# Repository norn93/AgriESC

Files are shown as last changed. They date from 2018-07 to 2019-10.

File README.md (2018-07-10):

# AgriESC
A brushless motor driver for small to medium sized motors

This project was forked from and inspired by antonchromjak's MINI4 (Mini VESC: https://github.com/antonchromjak/MINI4) and was practically copied from Benjamin Vedder's Brushless Motor Controller (VESC: https://github.com/vedderb/bldc-hardware). It is an attempt to build a slightly cheaper motor controller for 24 V/10 A motors.

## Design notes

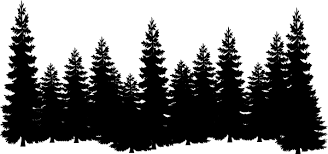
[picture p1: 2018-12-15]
images/forest.png

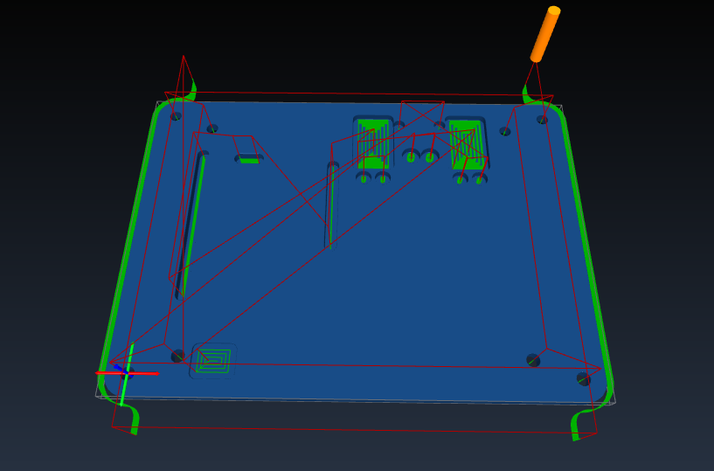
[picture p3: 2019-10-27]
gcode/Heatsink/heatsink.png

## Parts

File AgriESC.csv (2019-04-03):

Id | Designator | Package | Quantity | Designation | Supplier and ref
1 | R42,R43,R20,R21,R35 | R_0603_1608Metric_Pad1.05x0.95mm_HandSolder | 5 | 10k
2 | U16 | SOT-23-5 | 1 | MCP6001-OT
3 | USB | CONN-10118194-0001LF-FCI3 | 1 | USB_OTG
4 | C7,C8 | CP_Radial_D10.0mm_P5.00mm_Side_Mounted | 2 | 680u_35V
5 | R25 | R_0603_1608Metric_Pad1.05x0.95mm_HandSolder | 1 | 0R
6 | R26,R28 | R_0603_1608Metric_Pad1.05x0.95mm_HandSolder | 2 | 22R
7 | REF**,REF**,REF**,REF** | MountingHole_3.2mm_M3_Pad_Via | 4 | MountingHole_3.2mm_M3_Pad_Via
8 | SWD | JST_PA_01x05 | 1 | SWD
9 | COMM | JST_PA_01x08 | 1 | COMM
10 | C27,C12,C13,C14,C15,C16,C26 | C_0603_1608Metric_Pad1.05x0.95mm_HandSolder | 7 | 100n
11 | HALL ENCODERS | JST_PA_01x06 | 1 | HALL_ENC
12 | CAN | JST_PA_01x04 | 1 | CAN
13 | U1,U2,U3,U4,U5,U6 | FDMS7698 | 6 | FDMS7698
14 | GPIO | JST_PA_01x06 | 1 | GPIO
15 | U15,U14 | SOT-23 | 2 | MCP1700-3302E_SOT23
16 | U10 | LQFP-64_10x10mm_P0.5mm | 1 | STM32F405RGT6
17 | D2 | LED_0603_1608Metric_Pad1.05x0.95mm_HandSolder | 1 | GREEN
18 | Y1 | CSTNE8M00G550000R0 | 1 | 8M Resonator
19 | C1,C2,C3,C4,C5,C6,C41 | C_0805_2012Metric_Pad1.15x1.40mm_HandSolder | 7 | 4u7_35V
20 | C9,C10,C11 | C_0603_1608Metric_Pad1.05x0.95mm_HandSolder | 3 | 0.1u
21 | C17,C18,C19,C20,C21,C25,C28,C29,C30 | C_0603_1608Metric_Pad1.05x0.95mm_HandSolder | 9 | 2u2
22 | C22,C23,C24 | C_0603_1608Metric_Pad1.05x0.95mm_HandSolder | 3 | 4n7
23 | C31,C33,C36 | C_0603_1608Metric_Pad1.05x0.95mm_HandSolder | 3 | 100n_16V
24 | C32 | C_0603_1608Metric_Pad1.05x0.95mm_HandSolder | 1 | 22n_50V
25 | C34 | C_0603_1608Metric_Pad1.05x0.95mm_HandSolder | 1 | 2u2_16V
26 | C35 | C_0603_1608Metric_Pad1.05x0.95mm_HandSolder | 1 | 220n_16V
27 | C37 | C_0603_1608Metric_Pad1.05x0.95mm_HandSolder | 1 | 100n_6V3
28 | C38 | C_0603_1608Metric_Pad1.05x0.95mm_HandSolder | 1 | 1u_6V3
29 | C39,C46 | C_0603_1608Metric_Pad1.05x0.95mm_HandSolder | 2 | 100n_10V
30 | C40 | C_0603_1608Metric_Pad1.05x0.95mm_HandSolder | 1 | 1u_10V
31 | C42 | C_0603_1608Metric_Pad1.05x0.95mm_HandSolder | 1 | 470n_35V
32 | C43,C44,C49,C51 | C_0603_1608Metric_Pad1.05x0.95mm_HandSolder | 4 | 2u2_5V
33 | C45 | C_0603_1608Metric_Pad1.05x0.95mm_HandSolder | 1 | 100n_5V
34 | C47 | C_0603_1608Metric_Pad1.05x0.95mm_HandSolder | 1 | 2u2_35V
35 | C48 | C_0603_1608Metric_Pad1.05x0.95mm_HandSolder | 1 | 10u_5V
36 | C50,C52 | C_0603_1608Metric_Pad1.05x0.95mm_HandSolder | 2 | 2u2_3V3
37 | D1 | LED_0603_1608Metric_Pad1.05x0.95mm_HandSolder | 1 | BLUE
38 | D3 | LED_0603_1608Metric_Pad1.05x0.95mm_HandSolder | 1 | RED
39 | D4 | D_SOD-123F | 1 | D_Schottky_40V_1A
40 | J1 | XT30PW-F | 1 | SUPPLY
41 | A | SolderWirePad_1x01_SMD_5x10mm | 1 | PH_A
42 | B | SolderWirePad_1x01_SMD_5x10mm | 1 | PH_B
43 | C | SolderWirePad_1x01_SMD_5x10mm | 1 | PH_C
44 | SERVO | JST_PA_01x03 | 1 | SERVO
45 | L1 | NR8040T220M | 1 | 22u
46 | R1,R2,R3,R10,R11,R12 | R_0603_1608Metric_Pad1.05x0.95mm_HandSolder | 6 | 4R7
47 | R4,R5,R6 | R_2512_6332Metric_Pad1.52x3.35mm_HandSolder | 3 | 0.004R
48 | R7,R8,R9 | R_0603_1608Metric_Pad1.05x0.95mm_HandSolder | 3 | 59k
49 | R13,R14,R15 | R_0603_1608Metric_Pad1.05x0.95mm_HandSolder | 3 | 1k
50 | R16,R17,R18,R22 | R_0603_1608Metric_Pad1.05x0.95mm_HandSolder | 4 | 100R
51 | R19 | R_0603_1608Metric_Pad1.05x0.95mm_HandSolder | 1 | 10k_NTC
52 | R23,R24 | R_0603_1608Metric_Pad1.05x0.95mm_HandSolder | 2 | 150R
53 | R27,R31,R36,R39 | R_0603_1608Metric_Pad1.05x0.95mm_HandSolder | 4 | 47k
54 | R29 | R_0603_1608Metric_Pad1.05x0.95mm_HandSolder | 1 | 220R
55 | R30,R32,R38,R40 | R_0603_1608Metric_Pad1.05x0.95mm_HandSolder | 4 | 5k6
56 | R33,R34,R37 | R_0603_1608Metric_Pad1.05x0.95mm_HandSolder | 3 | 2k2
57 | R41 | R_0603_1608Metric_Pad1.05x0.95mm_HandSolder | 1 | 100k
58 | U7,U8,U9 | MAX9920 | 3 | MAX9920
59 | U11 | DRV8303 | 1 | DRV8303
60 | U13 | SOT-23-6 | 1 | LMR16006YQ5
61 | U12 | DFN-8-1EP_3x3mm_Pitch0.65mm | 1 | TJA1051TK-3
62 | NT1,NT2,NT3 | NetTie-2_SMD_Pad0.5mm | 3 | Net-Tie_2
63 | SW1 | SolderJumper-3_P1.3mm_Open_RoundedPad1.0x1.5mm_NumberLabels | 1 | SW_SPDT
64 | REF** | OSHW-Logo_7.5x8mm_SilkScreen | 1 | OSHW-Logo_7.5x8mm_SilkScreen
65 | G*** | LOGO3 | 1 | LOGO3

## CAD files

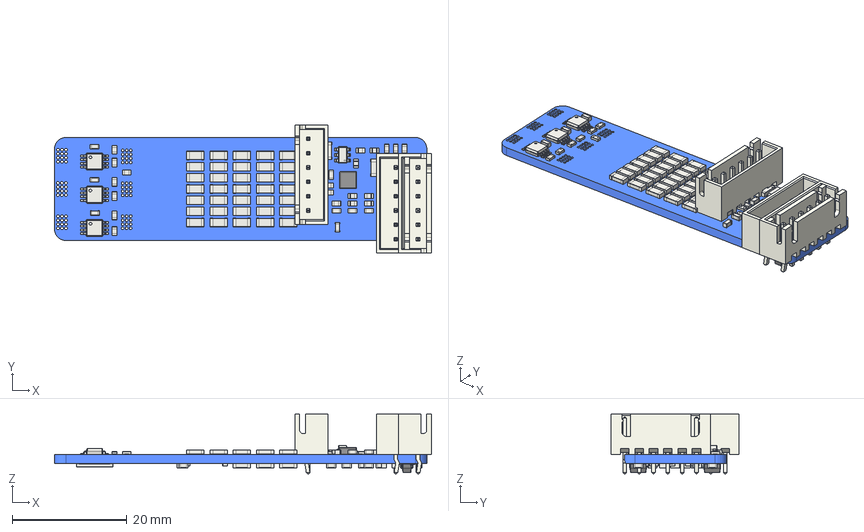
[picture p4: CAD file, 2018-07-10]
mini4/MINI_VESC.FCStd
65.8 x 22.4 x 10.4 mm
Pcb
C_1206_
R_0603_
C_0603_
R_0603_001
R_0603_002
R_0603_003
C_0603_001
R_0603_004
R_0603_005
C_1206_001
C_1206_002
C_1206_003
C_1206_004
C_1206_005
C_1206_006
C_1206_007
C_1206_008
C_1206_009
C_1206_010
C_1206_011
C_1206_012
C_1206_013
C_1206_014
C_1206_015
C_1206_016
C_1206_017
C_1206_018
C_1206_019
C_1206_020
C_1206_021
C_1206_022
C_1206_023
C_1206_024
C_1206_025
C_1206_026
C_1206_027
C_1206_028
C_1206_029
C_1206_030
C_1206_031
C_1206_032
C_1206_033
C_1206_034
C_1206_035
C_1206_036
C_1206_037
C_0603_002
C_0603_003
R_0603_006
R_0603_007
R_0603_008
R_0603_009
R_0603_010
R_0603_011
SOT_23_6_
R_0603_012
R_0603_013
C_1206_038
C_1206_039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

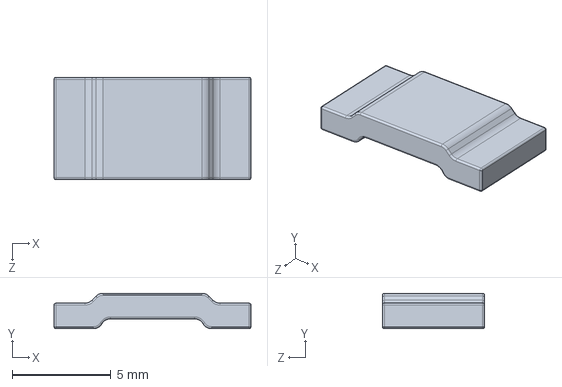
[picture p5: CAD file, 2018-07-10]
mini4_3dmodels/3921_RESISTOR.STEP
10.0 x 1.80 x 5.20 mm

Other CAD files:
mini4_3dmodels/user library-pqfn 5x6.wrl.sldprt
mini4_3dmodels/pqfn 5x6.wrl.sldprt

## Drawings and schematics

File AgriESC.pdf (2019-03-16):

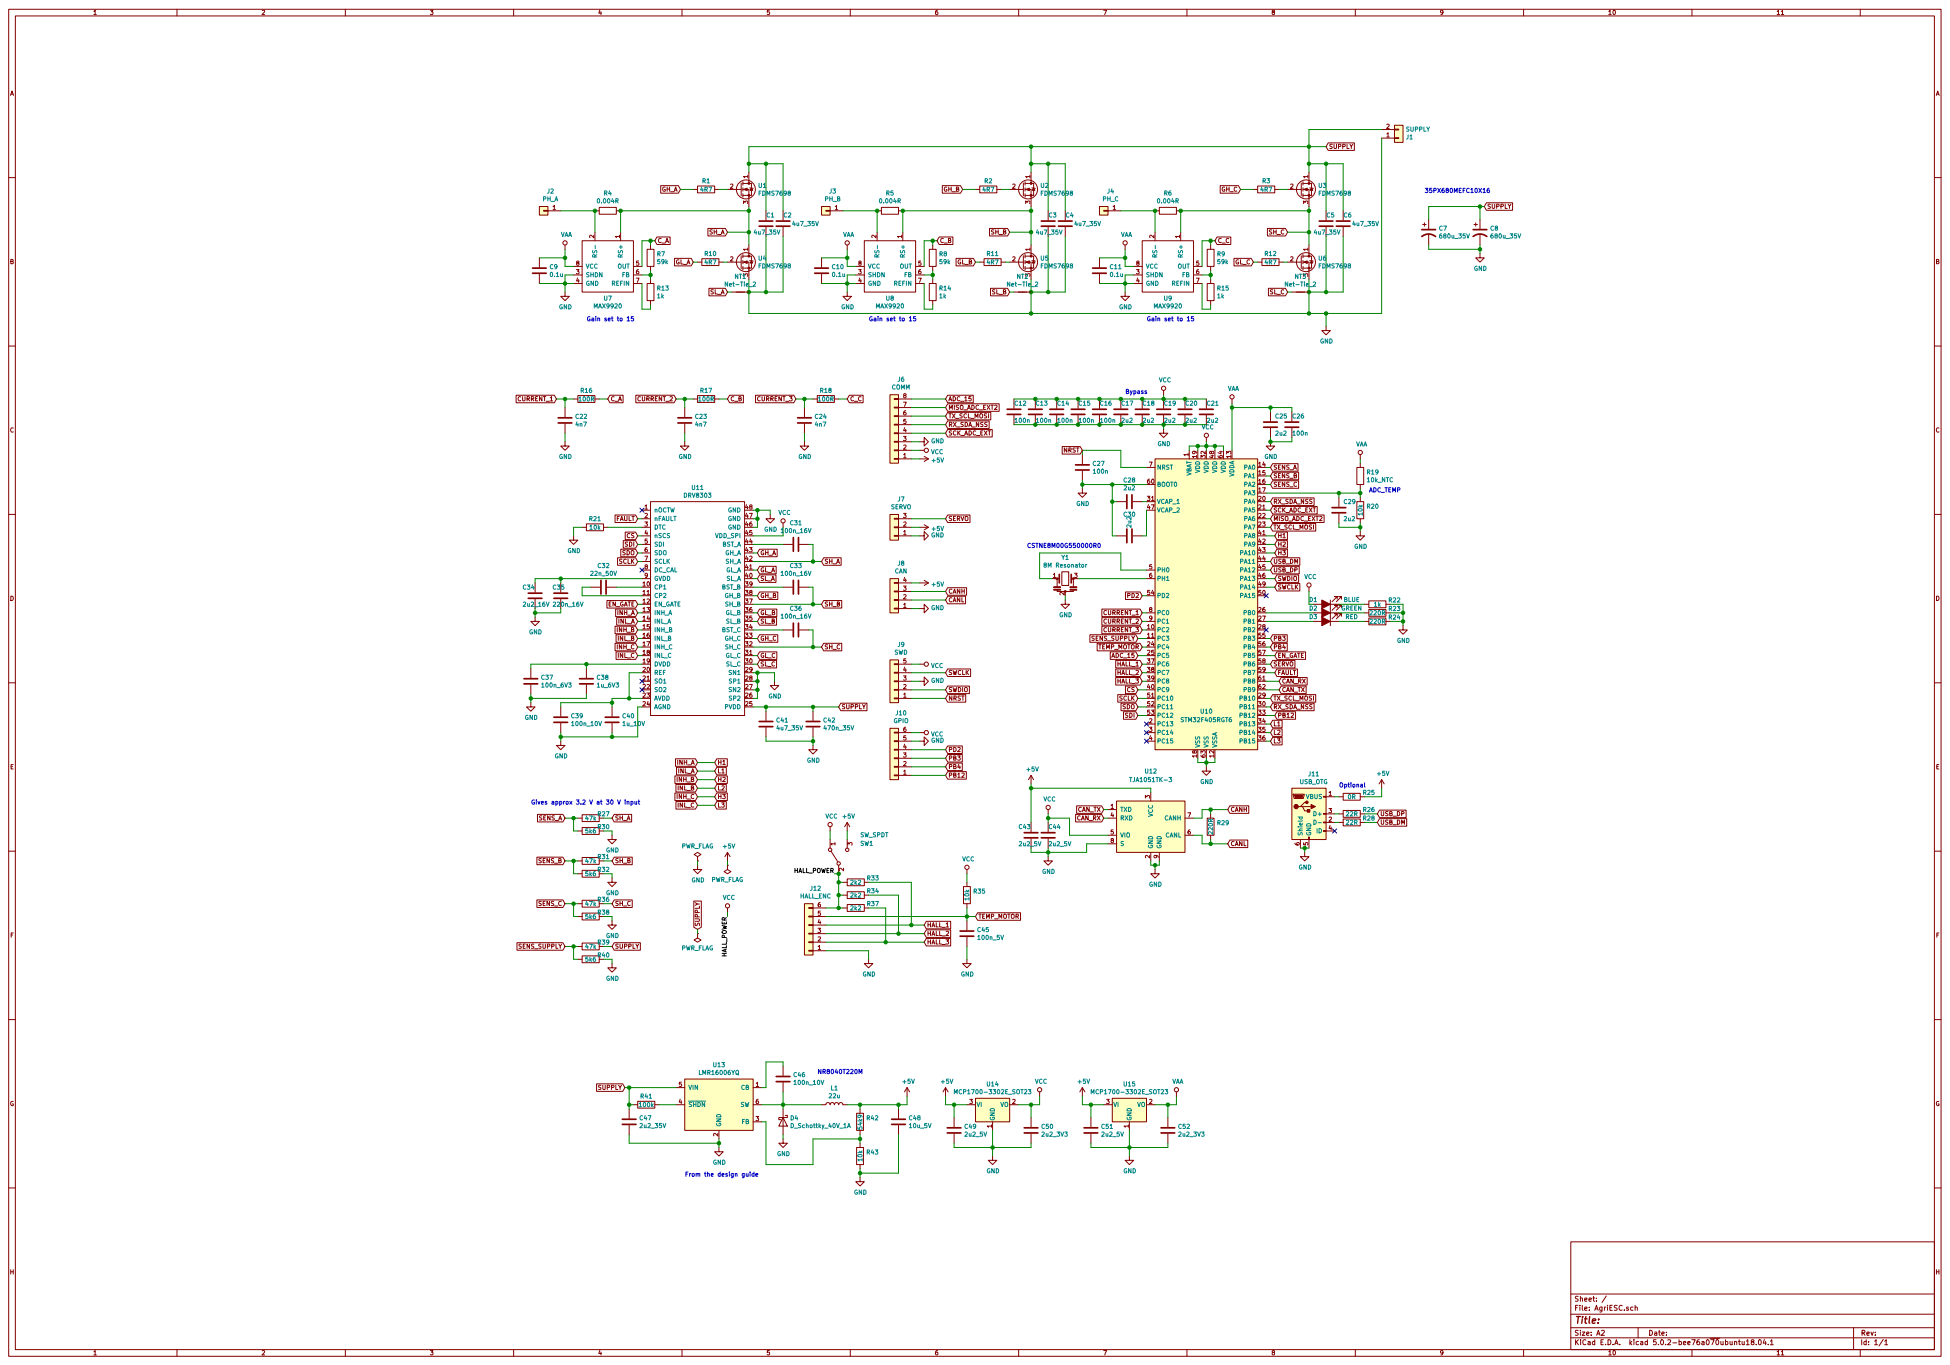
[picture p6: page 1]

PD2 PB3 PB4 PB12 +5V GND GND Gives approx 3.2 V at 30 V input C37

File: AgriESC.sch Sheet: /

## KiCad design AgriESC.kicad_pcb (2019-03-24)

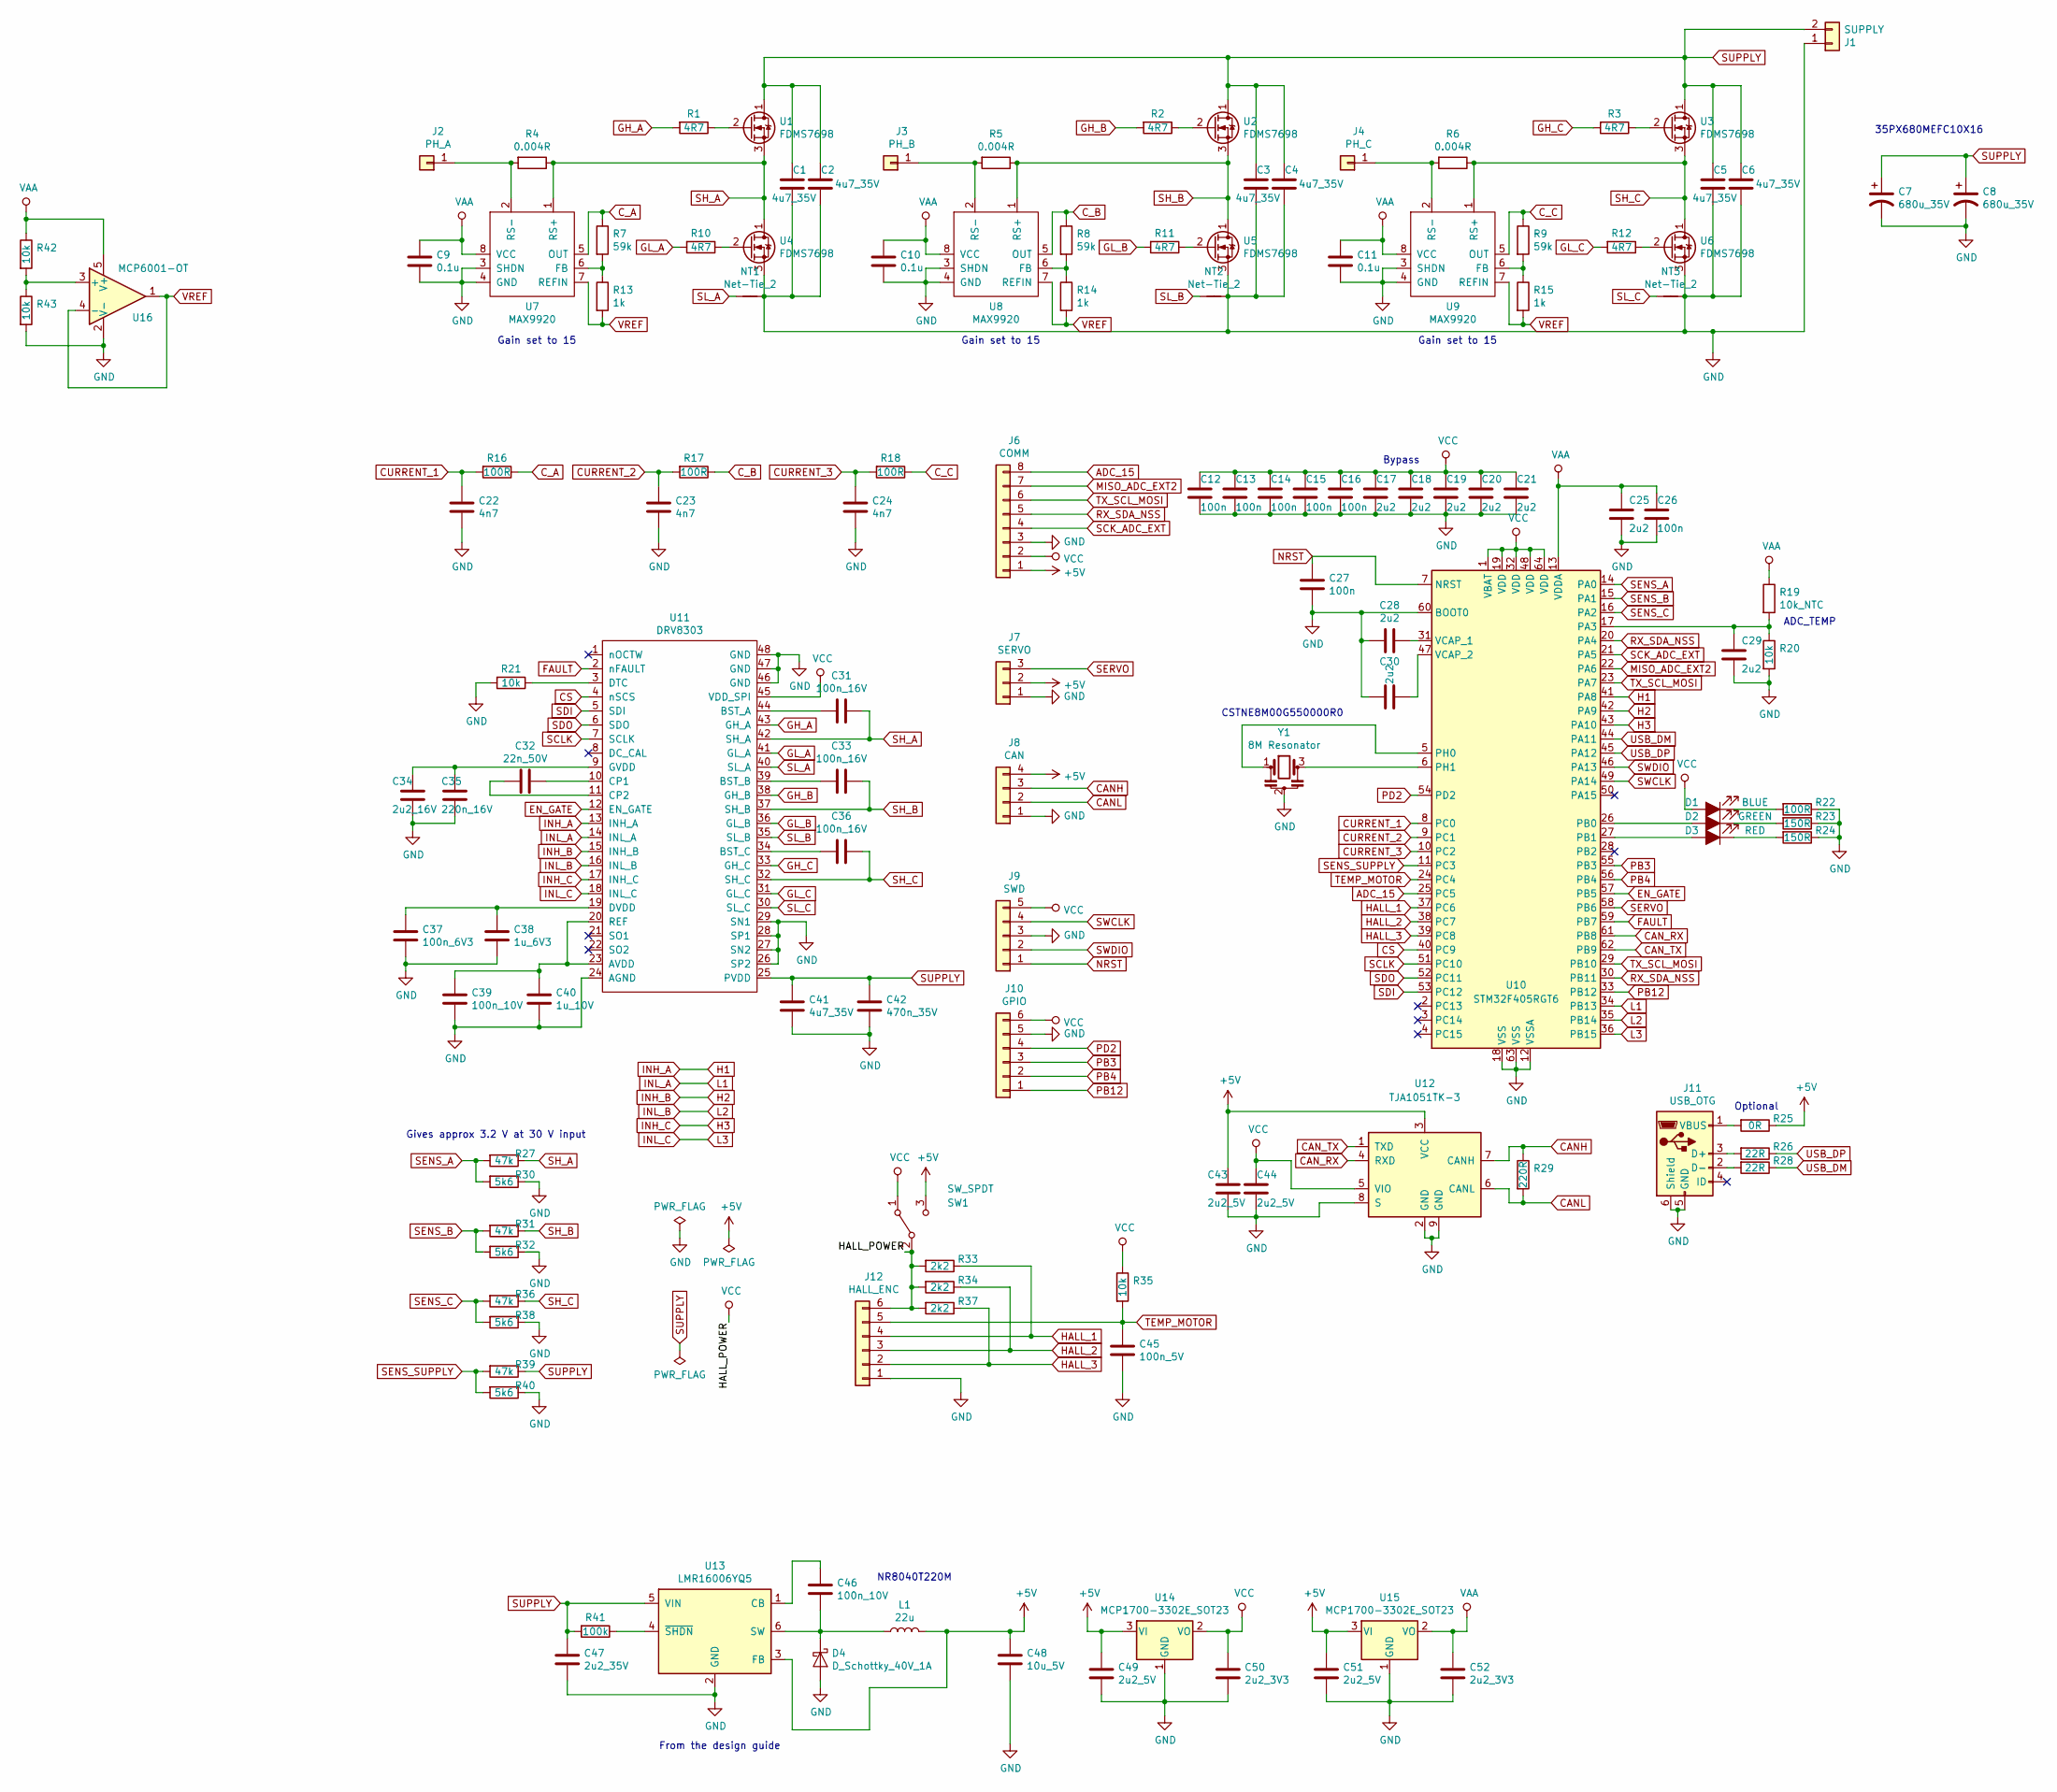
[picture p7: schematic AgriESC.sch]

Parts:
C1, C2, C3, C4, C5, C6, C41: 4u7_35V; C_0805_2012Metric_Pad1.15x1.40mm_HandSolder
C7, C8: 680u_35V; CP_Radial_D10.0mm_P5.00mm_Side_Mounted
C9, C10, C11: 0.1u; C_0603_1608Metric_Pad1.05x0.95mm_HandSolder
C12, C13, C14, C15, C16, C26, C27: 100n; C_0603_1608Metric_Pad1.05x0.95mm_HandSolder
C17, C18, C19, C20, C21, C25, C28, C29, C30: 2u2; C_0603_1608Metric_Pad1.05x0.95mm_HandSolder
C22, C23, C24: 4n7; C_0603_1608Metric_Pad1.05x0.95mm_HandSolder
C31, C33, C36: 100n_16V; C_0603_1608Metric_Pad1.05x0.95mm_HandSolder
C32: 22n_50V; C_0603_1608Metric_Pad1.05x0.95mm_HandSolder
C34: 2u2_16V; C_0603_1608Metric_Pad1.05x0.95mm_HandSolder
C35: 220n_16V; C_0603_1608Metric_Pad1.05x0.95mm_HandSolder
C37: 100n_6V3; C_0603_1608Metric_Pad1.05x0.95mm_HandSolder
C38: 1u_6V3; C_0603_1608Metric_Pad1.05x0.95mm_HandSolder
C39, C46: 100n_10V; C_0603_1608Metric_Pad1.05x0.95mm_HandSolder
C40: 1u_10V; C_0603_1608Metric_Pad1.05x0.95mm_HandSolder
C42: 470n_35V; C_0603_1608Metric_Pad1.05x0.95mm_HandSolder
C43, C44, C49, C51: 2u2_5V; C_0603_1608Metric_Pad1.05x0.95mm_HandSolder
C45: 100n_5V; C_0603_1608Metric_Pad1.05x0.95mm_HandSolder
C47: 2u2_35V; C_0603_1608Metric_Pad1.05x0.95mm_HandSolder
C48: 10u_5V; C_0603_1608Metric_Pad1.05x0.95mm_HandSolder
C50, C52: 2u2_3V3; C_0603_1608Metric_Pad1.05x0.95mm_HandSolder
D1: BLUE; LED_0603_1608Metric_Pad1.05x0.95mm_HandSolder
D2: GREEN; LED_0603_1608Metric_Pad1.05x0.95mm_HandSolder
D3: RED; LED_0603_1608Metric_Pad1.05x0.95mm_HandSolder
D4: D_Schottky_40V_1A; D_SOD-123F
J1: SUPPLY; XT30PW-F
J2: PH_A; SolderWirePad_1x01_SMD_5x10mm
J3: PH_B; SolderWirePad_1x01_SMD_5x10mm
J4: PH_C; SolderWirePad_1x01_SMD_5x10mm
J6: COMM; JST_PA_01x08
J7: SERVO; JST_PA_01x03
J8: CAN; JST_PA_01x04
J9: SWD; JST_PA_01x05
J10: GPIO; JST_PA_01x06
J11: USB_OTG; CONN-10118194-0001LF-FCI3
J12: HALL_ENC; JST_PA_01x06
L1: 22u; NR8040T220M
NT1, NT2, NT3: Net-Tie_2; NetTie-2_SMD_Pad0.5mm
R1, R2, R3, R10, R11, R12: 4R7; R_0603_1608Metric_Pad1.05x0.95mm_HandSolder
R4, R5, R6: 0.004R; R_2512_6332Metric_Pad1.52x3.35mm_HandSolder
R7, R8, R9: 59k; R_0603_1608Metric_Pad1.05x0.95mm_HandSolder
R13, R14, R15: 1k; R_0603_1608Metric_Pad1.05x0.95mm_HandSolder
R16, R17, R18, R22: 100R; R_0603_1608Metric_Pad1.05x0.95mm_HandSolder
R19: 10k_NTC; R_0603_1608Metric_Pad1.05x0.95mm_HandSolder
R20, R21, R35, R42, R43: 10k; R_0603_1608Metric_Pad1.05x0.95mm_HandSolder
R23, R24: 150R; R_0603_1608Metric_Pad1.05x0.95mm_HandSolder
R25: 0R; R_0603_1608Metric_Pad1.05x0.95mm_HandSolder
R26, R28: 22R; R_0603_1608Metric_Pad1.05x0.95mm_HandSolder
R27, R31, R36, R39: 47k; R_0603_1608Metric_Pad1.05x0.95mm_HandSolder
R29: 220R; R_0603_1608Metric_Pad1.05x0.95mm_HandSolder
R30, R32, R38, R40: 5k6; R_0603_1608Metric_Pad1.05x0.95mm_HandSolder
R33, R34, R37: 2k2; R_0603_1608Metric_Pad1.05x0.95mm_HandSolder
R41: 100k; R_0603_1608Metric_Pad1.05x0.95mm_HandSolder
SW1: SW_SPDT; SolderJumper-3_P1.3mm_Open_RoundedPad1.0x1.5mm_NumberLabels
U1, U2, U3, U4, U5, U6: FDMS7698
U7, U8, U9: MAX9920
U10: STM32F405RGT6; LQFP-64_10x10mm_P0.5mm
U11: DRV8303
U12: TJA1051TK-3; DFN-8-1EP_3x3mm_Pitch0.65mm
U13: LMR16006YQ5; SOT-23-6
U14, U15: MCP1700-3302E_SOT23; SOT-23
U16: MCP6001-OT; SOT-23-5
Y1: 8M Resonator; CSTNE8M00G550000R0

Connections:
+5V: C43.1, C48.1, C49.1, C51.1, J6.1, J7.2, J8.4, L1.2, R25.1, SW1.3 (C), U12.3 (VCC), U13.3 (FB), U14.3 (VI), U15.3 (VI); also elsewhere on the board
ADC_15: J6.8, U10.25 (PC5); also elsewhere on the board
CANH: J8.3, R29.1, U12.7 (CANH); also elsewhere on the board
CANL: J8.2, R29.2, U12.6 (CANL); also elsewhere on the board
CAN_RX: U10.61 (PB8), U12.4 (RXD)
CAN_TX: U10.62 (PB9), U12.1 (TXD)
CS: U10.40 (PC9), U11.4 (nSCS)
CURRENT_1: C22.1, R16.2, U10.8 (PC0)
CURRENT_2: C23.1, R17.2, U10.9 (PC1)
CURRENT_3: C24.1, R18.2, U10.10 (PC2)
C_A: R7.1, R16.1, U7.5 (OUT)
C_B: R8.1, R17.1, U8.5 (OUT)
C_C: R9.1, R18.1, U9.5 (OUT)
EN_GATE: U10.57 (PB5), U11.12 (EN_GATE)
FAULT: U10.59 (PB7), U11.2 (nFAULT)
GH_A: R1.2, U11.43 (GH_A)
GH_B: R2.2, U11.38 (GH_B)
GH_C: R3.2, U11.33 (GH_C)
GL_A: R10.2, U11.41 (GL_A)
GL_B: R11.2, U11.36 (GL_B)
GL_C: R12.2, U11.31 (GL_C)
GND: C1.2, C2.2, C3.2, C4.2, C5.2, C6.2, C7.2, C8.2, C9.2, C10.2, C11.2, C12.2, C13.2, C14.2, C15.2, C16.2, C17.2, C18.2, C19.2, C20.2, C21.2, C22.2, C23.2, C24.2, C25.2, C26.2, C27.2, C28.2, C29.2, C30.2, C34.2, C35.2, C37.2, C38.2, C39.2, C40.2, C41.2, C42.2, C43.2, C44.2, C45.2, C47.2, C48.2, C49.2, C50.2, C51.2, C52.2, D4.2 (A), J1.1, J6.3, J7.1, J8.1, J9.3, J10.5, J11.5 (GND), J11.6 (Shield), J12.1, NT1.1, NT2.1, NT3.1, R20.2, R21.2, R22.1, R23.1, R24.1, R30.1, R32.1, R38.1, R40.1, R43.2, U4.3 (S), U5.3 (S), U6.3 (S), U7.3 (SHDN), U7.4 (GND), U8.3 (SHDN), U8.4 (GND), U9.3 (SHDN), U9.4 (GND), U10.12 (VSSA), U10.18 (VSS), U10.60 (BOOT0), U10.63 (VSS), U11.24 (AGND), U11.26 (SP2), U11.27 (SN2), U11.28 (SP1), U11.29 (SN1), U11.46 (GND), U11.47 (GND), U11.48 (GND), U12.2 (GND), U12.8 (S), U12.9 (GND), U13.2 (GND), U14.1 (GND), U15.1 (GND), U16.2 (V-), Y1.2; also elsewhere on the board
H1: U10.41 (PA8), U11.13 (INH_A)
H2: U10.42 (PA9), U11.15 (INH_B)
H3: U10.43 (PA10), U11.17 (INH_C)
HALL_1: J12.4, R33.1, U10.37 (PC6); also elsewhere on the board
HALL_2: J12.3, R34.1, U10.38 (PC7); also elsewhere on the board
HALL_3: J12.2, R37.1, U10.39 (PC8); also elsewhere on the board
INL_A: U10.34 (PB13), U11.14 (INL_A)
INL_B: U10.35 (PB14), U11.16 (INL_B)
INL_C: U10.36 (PB15), U11.18 (INL_C)
MISO_ADC_EXT2: J6.7, U10.22 (PA6); also elsewhere on the board
NRST: C27.1, J9.1, U10.7 (NRST); also elsewhere on the board
unnamed: C28.1, U10.31 (VCAP_1)
unnamed: C29.1, R19.2, R20.1, U10.17 (PA3)
unnamed: C30.1, U10.47 (VCAP_2)
unnamed: C31.2, U11.44 (BST_A)
unnamed: C32.1, U11.10 (CP1)
unnamed: C32.2, U11.11 (CP2)
unnamed: C33.2, U11.39 (BST_B)
unnamed: C34.1, C35.1, U11.9 (GVDD)
unnamed: C36.2, U11.34 (BST_C)
unnamed: C37.1, C38.1, U11.19 (DVDD)
unnamed: C39.1, C40.1, U11.20 (REF), U11.23 (AVDD)
unnamed: C46.1, D4.1 (K), L1.1, U13.6 (SW)
unnamed: C46.2, U13.1 (CB)
unnamed: D1.1 (K), R22.2
unnamed: D2.1 (K), R23.2
unnamed: D2.2 (A), U10.26 (PB0)
unnamed: D3.1 (K), R24.2
unnamed: D3.2 (A), U10.27 (PB1)
unnamed 51: J2.1, R4.2, U7.2 (RS-); also elsewhere on the board
unnamed 52: J3.1, R5.2, U8.2 (RS-); also elsewhere on the board
unnamed 53: J4.1, R6.2, U9.2 (RS-); also elsewhere on the board
unnamed 54: J11.1 (VBUS), R25.2; also elsewhere on the board
unnamed 55: J11.2 (D-), R28.2; also elsewhere on the board
unnamed 56: J11.3 (D+), R26.2; also elsewhere on the board
unnamed: R1.1, U1.2 (G)
unnamed: R2.1, U2.2 (G)
unnamed: R3.1, U3.2 (G)
unnamed: R10.1, U4.2 (G)
unnamed: R11.1, U5.2 (G)
unnamed: R12.1, U6.2 (G)
unnamed: R7.2, R13.1, U7.6 (FB)
unnamed: R8.2, R14.1, U8.6 (FB)
unnamed: R9.2, R15.1, U9.6 (FB)
unnamed: R21.1, U11.3 (DTC)
unnamed: R41.1, U13.4 (~SHDN)
unnamed: R42.2, R43.1, U16.3 (+)
unnamed: U10.5 (PH0), Y1.1
unnamed: U10.6 (PH1), Y1.3
PB3: J10.3, U10.55 (PB3); also elsewhere on the board
PB4: J10.2, U10.56 (PB4); also elsewhere on the board
PB12: J10.1, U10.33 (PB12); also elsewhere on the board
PD2: J10.4, U10.54 (PD2); also elsewhere on the board
RX_SDA_NSS: J6.5, U10.20 (PA4), U10.30 (PB11); also elsewhere on the board
SCK_ADC_EXT: J6.4, U10.21 (PA5); also elsewhere on the board
SCLK: U10.51 (PC10), U11.7 (SCLK)
SDI: U10.53 (PC12), U11.5 (SDI)
SDO: U10.52 (PC11), U11.6 (SDO)
SENS_A: R27.2, R30.2, U10.14 (PA0)
SENS_B: R31.2, R32.2, U10.15 (PA1)
SENS_C: R36.2, R38.2, U10.16 (PA2)
SENS_SUPPLY: R39.2, R40.2, U10.11 (PC3)
SERVO: J7.3, U10.58 (PB6); also elsewhere on the board
SH_A: C31.1, R4.1, R27.1, U1.3 (S), U4.1 (D), U7.1 (RS+), U11.42 (SH_A)
SH_B: C33.1, R5.1, R31.1, U2.3 (S), U5.1 (D), U8.1 (RS+), U11.37 (SH_B)
SH_C: C36.1, R6.1, R36.1, U3.3 (S), U6.1 (D), U9.1 (RS+), U11.32 (SH_C)
SL_A: NT1.2, U11.40 (SL_A)
SL_B: NT2.2, U11.35 (SL_B)
SL_C: NT3.2, U11.30 (SL_C)
SUPPLY: C1.1, C2.1, C3.1, C4.1, C5.1, C6.1, C7.1, C8.1, C41.1, C42.1, C47.1, J1.2, R39.1, R41.2, U1.1 (D), U2.1 (D), U3.1 (D), U11.25 (PVDD), U13.5 (VIN)
SWCLK: J9.4, U10.49 (PA14); also elsewhere on the board
SWDIO: J9.2, U10.46 (PA13); also elsewhere on the board
TEMP_MOTOR: C45.1, J12.5, R35.2, U10.24 (PC4); also elsewhere on the board
TX_SCL_MOSI: J6.6, U10.23 (PA7), U10.29 (PB10); also elsewhere on the board
USB_DM: R28.1, U10.44 (PA11)
USB_DP: R26.1, U10.45 (PA12)
VAA: C9.1, C10.1, C11.1, C25.1, C26.1, C52.1, R19.1, R42.1, U7.8 (VCC), U8.8 (VCC), U9.8 (VCC), U10.13 (VDDA), U15.2 (VO), U16.5 (V+)
VCC: C12.1, C13.1, C14.1, C15.1, C16.1, C17.1, C18.1, C19.1, C20.1, C21.1, C44.1, C50.1, D1.2 (A), J6.2, J9.5, J10.6, J12.6, R33.2, R34.2, R35.1, R37.2, SW1.1 (A), SW1.2 (B), U10.1 (VBAT), U10.19 (VDD), U10.32 (VDD), U10.48 (VDD), U10.64 (VDD), U11.45 (VDD_SPI), U12.5 (VIO), U14.2 (VO); also elsewhere on the board
VREF: R13.2, R14.2, R15.2, U7.7 (REFIN), U8.7 (REFIN), U9.7 (REFIN), U16.1, U16.4 (-)

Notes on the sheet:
Bypass
Optional
Gain set to 15
ADC_TEMP
From the design guide
Gives approx 3.2 V at 30 V input
CSTNE8M00G550000R0
NR8040T220M
35PX680MEFC10X16

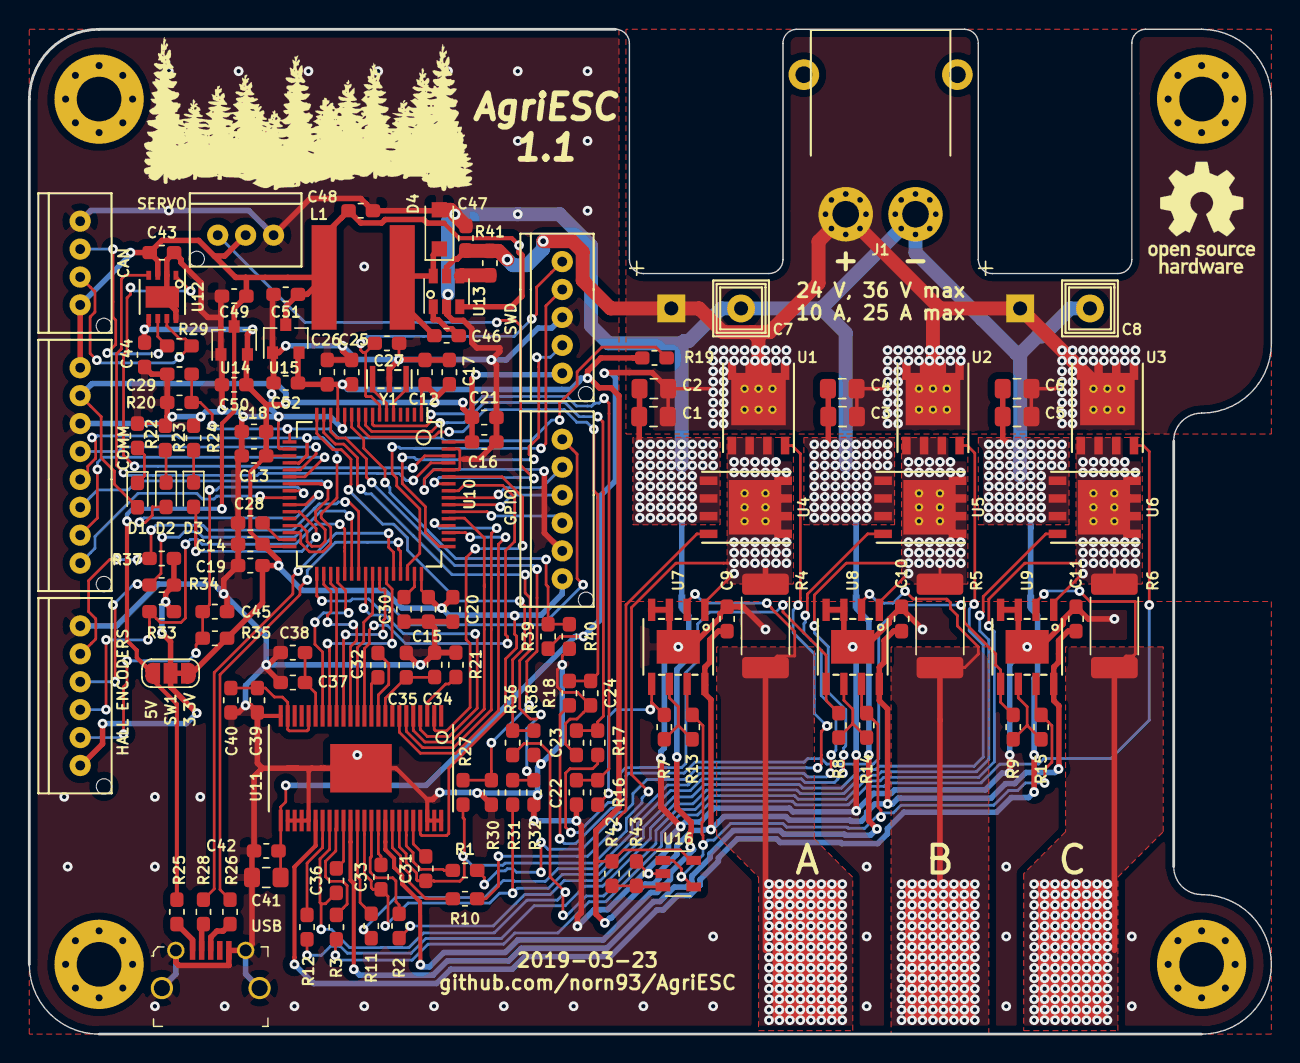
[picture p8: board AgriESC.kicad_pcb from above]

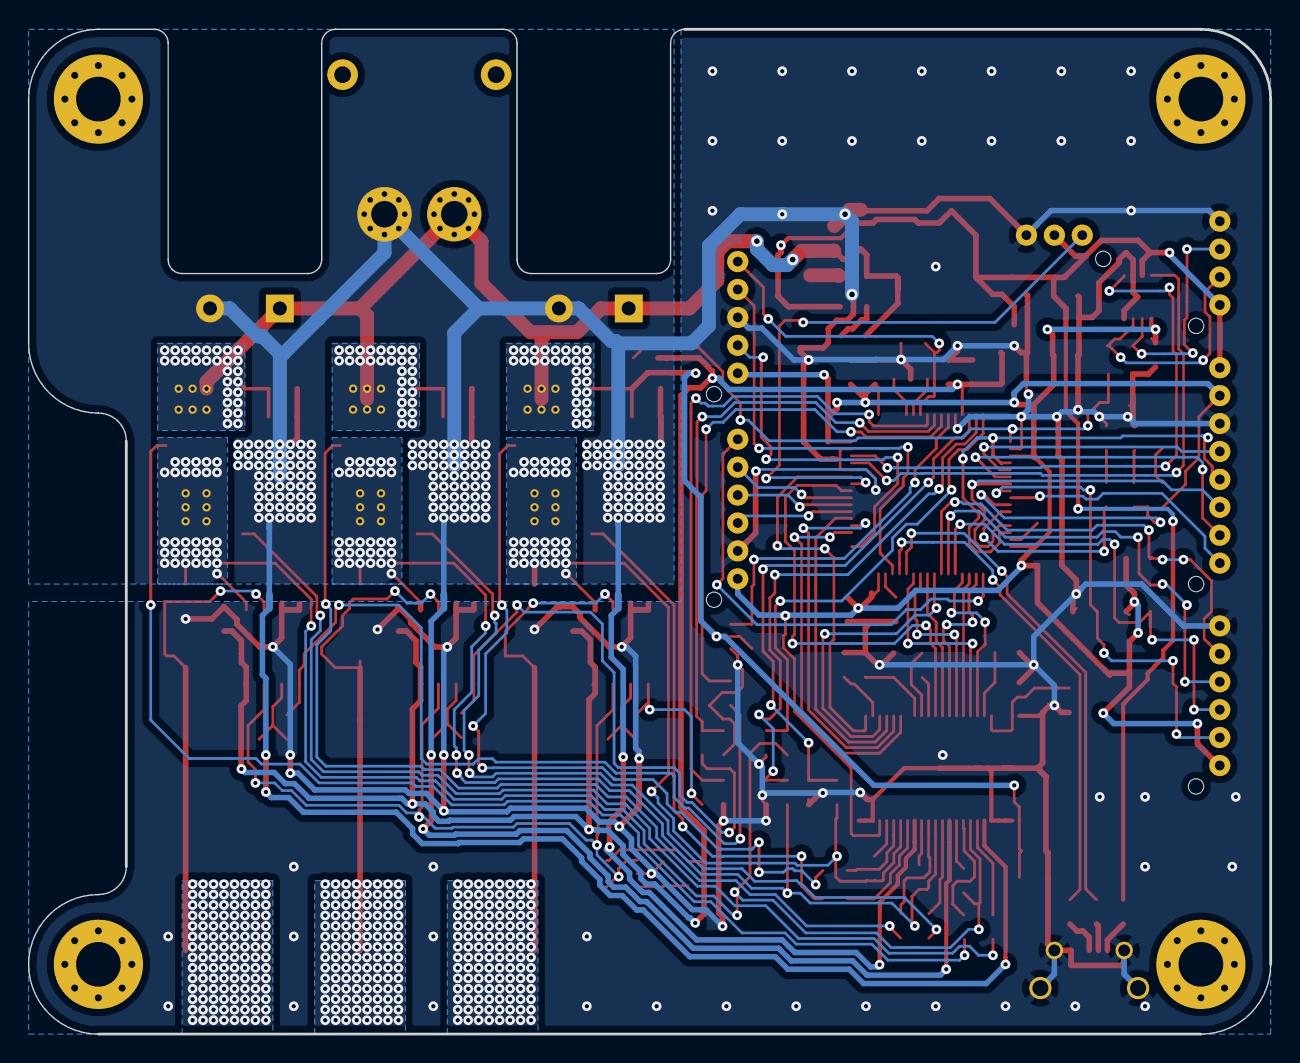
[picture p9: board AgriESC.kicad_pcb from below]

Board: 2 copper layers, 89.0 x 72.0 mm, 132 parts (3 on the bottom side), 101 nets.

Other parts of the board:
A: PH_A; SolderWirePad_1x01_SMD_5x10mm
B: PH_B; SolderWirePad_1x01_SMD_5x10mm
C: PH_C; SolderWirePad_1x01_SMD_5x10mm
CAN: CAN; JST_PA_01x04
COMM: COMM; JST_PA_01x08
GPIO: GPIO; JST_PA_01x06
HALL ENCODERS: HALL_ENC; JST_PA_01x06
SERVO: SERVO; JST_PA_01x03
SWD: SWD; JST_PA_01x05
USB: USB_OTG; CONN-10118194-0001LF-FCI3

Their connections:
+5V: CAN.4, COMM.1, SERVO.2; also elsewhere on the board
ADC_15: COMM.8; also elsewhere on the board
CANH: CAN.3; also elsewhere on the board
CANL: CAN.2; also elsewhere on the board
GND: CAN.1, COMM.3, GPIO.5, HALL ENCODERS.1, SERVO.1, SWD.3, USB.5, USB.6; also elsewhere on the board
HALL_1: HALL ENCODERS.4; also elsewhere on the board
HALL_2: HALL ENCODERS.3; also elsewhere on the board
HALL_3: HALL ENCODERS.2; also elsewhere on the board
MISO_ADC_EXT2: COMM.7; also elsewhere on the board
NRST: SWD.1; also elsewhere on the board
unnamed 51: A.1; also elsewhere on the board
unnamed 52: B.1; also elsewhere on the board
unnamed 53: C.1; also elsewhere on the board
unnamed 54: USB.1; also elsewhere on the board
unnamed 55: USB.2; also elsewhere on the board
unnamed 56: USB.3; also elsewhere on the board
PB3: GPIO.3; also elsewhere on the board
PB4: GPIO.2; also elsewhere on the board
PB12: GPIO.1; also elsewhere on the board
PD2: GPIO.4; also elsewhere on the board
RX_SDA_NSS: COMM.5; also elsewhere on the board
SCK_ADC_EXT: COMM.4; also elsewhere on the board
SERVO: SERVO.3; also elsewhere on the board
SWCLK: SWD.4; also elsewhere on the board
SWDIO: SWD.2; also elsewhere on the board
TEMP_MOTOR: HALL ENCODERS.5; also elsewhere on the board
TX_SCL_MOSI: COMM.6; also elsewhere on the board
VCC: COMM.2, GPIO.6, HALL ENCODERS.6, SWD.5; also elsewhere on the board

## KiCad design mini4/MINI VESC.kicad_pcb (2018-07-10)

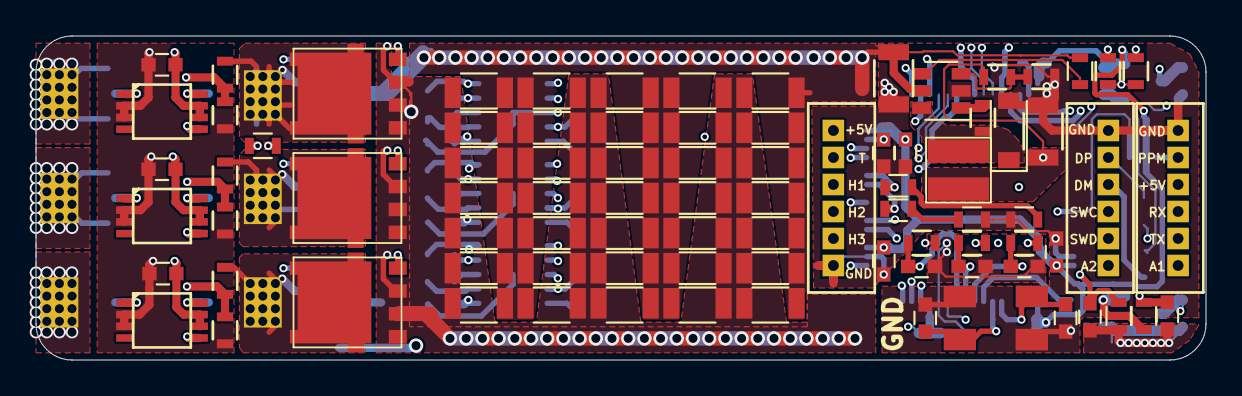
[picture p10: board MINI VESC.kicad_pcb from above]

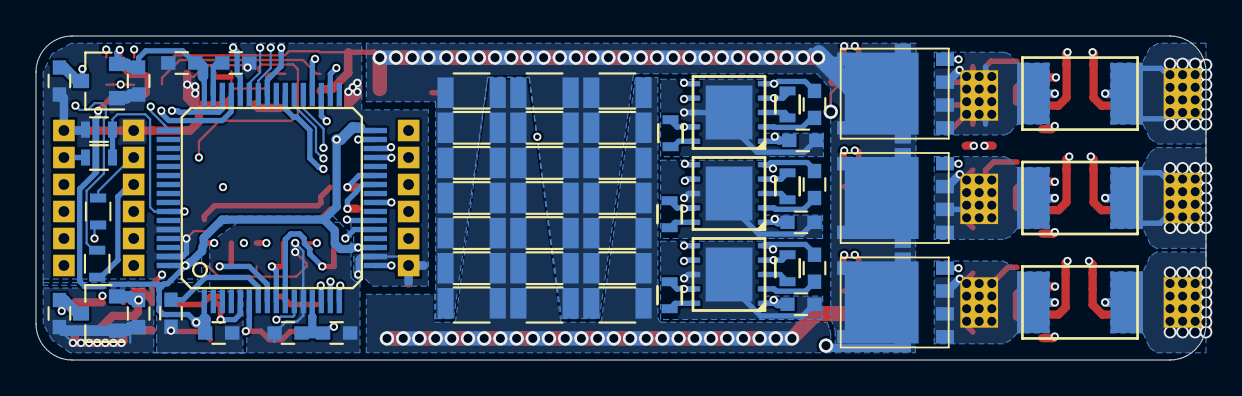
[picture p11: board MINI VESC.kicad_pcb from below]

Board: 4 copper layers, 65.0 x 18.0 mm, 151 parts (59 on the bottom side), 72 nets.

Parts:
C1, C2, C3: 220n; C_0603
C4, C5, C12, C13, C24, C25, C28, C32, C39, C48, C60, C61, C62, C63, C74, C75, C79, C82, C84, C85: 10u; R_1206
C6, C7, C8, C9, C10, C11, C17, C18, C19, C21, C22, C26, C27, C29, C77, C78, C86, C87, C88, C89, C90: 2u2; C_0603
C14, C15, C16: 4n7; C_0603
C20: 220nF; C_0603
C23: 220nF; R_0603
C30, C31: 10pF; C_0603
C33, C34, C35, C36, C37, C38, C40, C41, C42, C43, C44, C45, C46, C47, C49, C50, C51, C52, C53, C54, C55, C56, C57, C58, C59, C64, C65, C66, C67, C68, C69, C70, C71, C72, C73, C80, C81, C83: C; R_1206
C76: 100n; R_0603
D1: D_Schottky; D_SOD-123
D3, D4: LED; R_0603
L1: 22uH; WE-MAPI
P1, P2, P3, P4, P5, P6: CONN_1; prekov
P9, P10, P11: CONN_01X06; JST_ZH_1.5_6-Pin
Q1, Q2, Q3, Q4, Q5, Q6: Q_NMOS_GSD; DFN5
R1, R2, R3: RSENS; 2512Rv2
R4, R12, R14, R16: 25k5; R_0603
R5, R13, R15, R17: 2k2; R_0603
R6, R7, R8, R9, R10, R11: 7R5; R_0603
R18, R19, R20, R30: 100R; R_0603
R21: 510R; R_0603
R22: 8k; R_0603
R25, R27: 22R; R_0603
R28, R29: 220R; R_0603
R31, R33, R34: 10k; R_0603
R32: 10kNTC; R_0603
U1, U2, U3: LM5113; WSON10_
U4, U5, U6: AD8418; MSOP
U7: STM32F40X_LQFP64; lqfp64_pad_mod
U8: LMR16006; SOT-23-6
U9, U10: MCP1700; SOT-23
X1: CRYSTAL_SMD; 5x3.2KRISTALL

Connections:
+5V: C6.1, C7.1, C8.1, C25.2, C87.1, C89.1, L1.2, P9.1, P11.4, R22.1, U1.1, U2.1, U3.1, U9.3, U10.3
ADC_EXT1: P11.1, U7.21
ADC_EXT2: P10.1, U7.22
C1: C14.2, R18.2, U7.8
C2: C15.2, R19.2, U7.9
C3: C16.2, R20.2, U7.10
EN: R33.2, U8.4
HALL_1: P9.3, U7.37
HALL_2: P9.4, U7.38
HALL_3: P9.5, U7.39
HI1: U1.6, U7.41
HI2: U2.6, U7.42
HI3: U3.6, U7.43
I1: R18.1, U4.5
I2: R19.1, U5.5
I3: R20.1, U6.5
LED_GREEN: D3.2, U7.26
LED_RED: D4.2, U7.27
LI1: U1.7, U7.34
LI2: U2.7, U7.35
LI3: U3.7, U7.36
unnamed: C1.1, U1.2
unnamed: C2.1, U2.2
unnamed: C3.1, U3.2
unnamed: C17.2, U7.31
unnamed: C18.2, U7.47
unnamed: C20.2, U7.7
unnamed: C23.1, D1.1, L1.1, U8.6
unnamed: C23.2, U8.1
unnamed: C30.1, U7.5, X1.1
unnamed: C31.1, U7.6, X1.2
unnamed: C77.2, R31.2, R32.2, U7.17
unnamed: D3.1, R29.2
unnamed: D4.1, R28.2
unnamed: P1.1, R1.1, U4.1
unnamed: P2.1, R2.1, U5.1
unnamed: P3.1, R3.1, U6.1
unnamed: P10.4, R25.1
unnamed: P10.5, R27.1
unnamed: Q1.1, R6.1, U1.4
unnamed: Q2.1, R7.2, U1.9
unnamed: Q3.1, R8.1, U2.4
unnamed: Q4.1, R9.2, U2.9
unnamed: Q5.1, R10.1, U3.4
unnamed: Q6.1, R11.2, U3.9
unnamed: R6.2, U1.3
unnamed: R7.1, U1.10
unnamed: R8.2, U2.3
unnamed: R9.1, U2.10
unnamed: R10.2, U3.3
unnamed: R11.1, U3.10
unnamed: R21.2, R22.2, U8.3
RX: P11.3, U7.30
SENS_1: R12.1, R13.2, U7.14
SENS_2: R14.1, R15.2, U7.15
SENS_3: R16.1, R17.2, U7.16
SENS_SUPPLY: R4.2, R5.2, U7.11
SERVO: C76.2, R30.2, U7.58
SH1: C1.2, P4.1, Q1.2, Q2.3, R1.2, R12.2, U1.5, U4.8
SH2: C2.2, P5.1, Q3.2, Q4.3, R2.2, R14.2, U2.5, U5.8
SH3: C3.2, P6.1, Q5.2, Q6.3, R3.2, R16.2, U3.5, U6.8
SWCLK: P10.3, U7.49
SWDIO: P10.2, U7.46
TEMP_MOTOR: C78.2, P9.2, R34.2, U7.24
TX: P11.2, U7.29
USB-DM: R25.2, U7.44
USB-DP: R27.2, U7.45
VAA: C9.2, C10.2, C11.2, C19.1, C86.1, C90.1, R32.1, R34.1, U4.6, U4.7, U5.6, U5.7, U6.6, U6.7, U7.13, U10.2
VCC: C21.1, C22.1, C26.1, C27.1, C29.1, C88.1, U7.1, U7.19, U7.32, U7.48, U7.64, U9.2
VDD: C4.1, C5.1, C12.1, C13.1, C24.2, C28.1, C32.1, C33.1, C34.1, C35.1, C36.1, C37.1, C38.1, C39.1, C40.1, C41.1, C42.1, C43.1, C44.1, C45.1, C46.1, C47.1, C48.1, C49.1, C50.1, C51.1, C52.1, C53.1, C54.1, C55.1, C56.1, C57.1, C58.1, C59.1, C60.1, C61.1, C62.1, C63.1, C64.1, C65.1, C66.1, C67.1, C68.1, C69.1, C70.1, C71.1, C72.1, C73.1, C74.1, C75.1, C79.1, C80.1, C81.1, C82.1, C83.1, C84.1, C85.1, Q1.3, Q3.3, Q5.3, R4.1, R33.1, U8.5
VSS: C4.2, C5.2, C6.2, C7.2, C8.2, C9.1, C10.1, C11.1, C12.2, C13.2, C14.1, C15.1, C16.1, C17.1, C18.1, C19.2, C20.1, C21.2, C22.2, C24.1, C25.1, C26.2, C27.2, C28.2, C29.2, C30.2, C31.2, C32.2, C33.2, C34.2, C35.2, C36.2, C37.2, C38.2, C39.2, C40.2, C41.2, C42.2, C43.2, C44.2, C45.2, C46.2, C47.2, C48.2, C49.2, C50.2, C51.2, C52.2, C53.2, C54.2, C55.2, C56.2, C57.2, C58.2, C59.2, C60.2, C61.2, C62.2, C63.2, C64.2, C65.2, C66.2, C67.2, C68.2, C69.2, C70.2, C71.2, C72.2, C73.2, C74.2, C75.2, C76.1, C77.1, C78.1, C79.2, C80.2, C81.2, C82.2, C83.2, C84.2, C85.2, C86.2, C87.2, C88.2, C89.2, C90.2, D1.2, P9.6, P10.6, P11.6, Q2.2, Q4.2, Q6.2, R5.1, R13.1, R15.1, R17.1, R21.1, R28.1, R29.1, R31.1, U1.8, U2.8, U3.8, U4.2, U4.3, U5.2, U5.3, U6.2, U6.3, U7.12, U7.18, U7.60, U7.63, U8.2, U9.1, U10.1, X1.3
servoi: P11.5, R30.1

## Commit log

2018-07-10 Reorganising directory structure for new project
    [3921_RESISTOR.STEP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]
2018-07-10 Added microcontroller
    [AgriESC.kicad_pcb, AgriESC.sch]
2018-07-10 Added CAN, USB, hall sensors, servo
    [AgriESC.sch]
2018-07-10 Added document detailing current sense op amp comparison
2018-07-27 Started adding driver
    [AgriESC.sch]
2018-07-28 First draft of schematic complete
    [AgriESC.sch]
2018-07-29 Started allocating footprints
    [AgriESC.sch]
2018-07-31 Added MAX9920 footprint to schematic
    [AgriESC.sch]
2018-07-31 Created MAX9920 footprint in project library
2018-08-01 Added capacitor voltages, added bulk capacitors for battery power supply, changed crystal, added bypass capacitors for higher frequencies
    [AgriESC.sch]
2018-08-01 Added DRV8303 footprint
2018-08-02 Added footprints for slide switch and FET
2018-08-02 Updated footprints, added analog supply
    [AgriESC.sch]
2018-08-03 Updated footprints to include silkscreen
2018-08-03 Reset annotation
    [AgriESC.sch]
2018-08-03 Created draft net
    [AgriESC.sch]
2018-08-03 Added PA style JST connectors
2018-08-03 Added XT30PW-M battery connector
2018-08-03 Added USB connector
2018-08-03 Started PCB layout
2018-08-03 Updated schematic with new battery supply connector and more MPNs
    [AgriESC.sch]
2018-08-03 Corrected battery connector polarity
    [AgriESC.sch]
2018-08-03 Started work on high current PCB layout
    [AgriESC.kicad_pcb]
2018-08-05 Fixed footprint vias
2018-08-05 First draft of high current part
    [AgriESC.kicad_pcb]
2018-08-05 Added a via footprint for heat-sinking
2018-08-06 Added vias to footprint
2018-08-06 Backed up old PCB
2018-08-06 Added new inductor and resonator footprints
2018-08-06 Updated schematic with new components
    [AgriESC.sch]
2018-08-06 Updated PCB layout to be much more compact
    [AgriESC.kicad_pcb]
2018-08-06 Second draft of high current part of PCB complete
    [AgriESC.kicad_pcb]
2018-08-07 Adding current sense op amps
    [AgriESC.kicad_pcb]
2018-11-17 Routed FET side of board, and removed copper layer for heatsink
    [AgriESC.kicad_pcb]
2018-11-18 Updated resonator footprint to include silkscreen
    [AgriESC.sch]
2018-11-18 Arranged critical microcontroller components, started arranging driver components
    [AgriESC.kicad_pcb]
2018-11-26 Arranged 5V power stage according to layout guide
    [AgriESC.kicad_pcb]
2018-11-26 Wired up LDOs
    [AgriESC.kicad_pcb]
2018-11-26 Added USB wiring
    [AgriESC.kicad_pcb]
2018-11-26 Finished USB ground
    [AgriESC.kicad_pcb]
2018-11-26 Added CAN wiring
    [AgriESC.kicad_pcb]
2018-11-26 Fix to schematic
    [AgriESC.sch]
2018-11-26 Arranged hall sensors
    [AgriESC.kicad_pcb]
2018-11-26 Wiring for motor driver
    [AgriESC.kicad_pcb]
2018-11-26 Wiring for microprocessor
    [AgriESC.kicad_pcb]
2018-11-26 Started arranging components
    [AgriESC.kicad_pcb, _saved_AgriESC.sch]
2018-11-26 Working through the routing
    [AgriESC.kicad_pcb]
2018-11-27 PCB routing
    [AgriESC.kicad_pcb, _saved_AgriESC.sch]
2018-11-27 Before CAN package update
    [AgriESC.sch]
2018-11-27 More routing, and an adjustment to the USB connector shield/ground
    [AgriESC.kicad_pcb]
2018-12-01 Routed thermistor
    [AgriESC.kicad_pcb]
2018-12-01 Routing completed! Now cleaning up tracks and increasing width where appropriate
    [AgriESC.kicad_pcb]
2018-12-01 Widening important traces
    [AgriESC.kicad_pcb]
2018-12-02 Correcting boundary
    [AgriESC.kicad_pcb]
2018-12-02 Updated from schematic
    [AgriESC.kicad_pcb]
2018-12-02 Moved USB and added moutning points
    [AgriESC.kicad_pcb]
2018-12-02 Added more ground planes to digital section
    [AgriESC.kicad_pcb]
2018-12-02 Cleaning routing
    [AgriESC.kicad_pcb]
2018-12-02 Rotated caps
    [AgriESC.kicad_pcb]
2018-12-02 Stronger traces. Saving progress before trying to reduce board height
    [AgriESC.kicad_pcb]
2018-12-02 Trying to make board more compact by moving buck converter
    [AgriESC.kicad_pcb]
2018-12-15 Added a bunch of logos, and a simple footprint for a side-mounted electrolytic capacitor
2018-12-15 Version 1.0 completed
    [AgriESC.kicad_pcb, AgriESC.sch]
2018-12-16 Exported gerber files for fabrication
    [AgriESC-B.Cu.gbr, AgriESC-B.Mask.gbr, AgriESC-B.Paste.gbr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]
2019-03-16 Version 1
    [AgriESC.sch]
2019-03-16 Updated LED resistors
    [AgriESC.sch]
2019-03-16 Updated LMR16006YQ to fixed 5V version, removed feedback resistors
    [AgriESC.sch]
2019-03-16 Fixed earthing on LMR
    [AgriESC.kicad_pcb]
2019-03-16 Added some more vias
    [AgriESC.kicad_pcb]
2019-03-16 Updated USB footprint
    [AgriESC.sch]
2019-03-23 Added new MAX9920 VREFIN
    [AgriESC.sch]
2019-03-23 Multiple small changes, all PCB layout related
    [AgriESC.kicad_pcb]
2019-03-23 Version 1.1
    [AgriESC-ALL.drl, AgriESC-B_Cu.gbr, AgriESC-B_Mask.gbr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]
2019-03-24 Added IBOM 1.1
    [AgriESC.kicad_pcb]
2019-10-03 Added gcode for making top and bottom of case
2019-10-27 New gcode for cutting heatsink
